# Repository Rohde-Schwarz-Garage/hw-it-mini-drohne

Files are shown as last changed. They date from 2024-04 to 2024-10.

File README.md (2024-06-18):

# BAUEN EINER KLEINEN DROHNE :helicopter:
<!--- Trennbalken bei Überschriften Level 1 (#) + kann kopiert werden --->


<!--- Hier kommt ein schönes Bild + ggf. mehr im Text --->
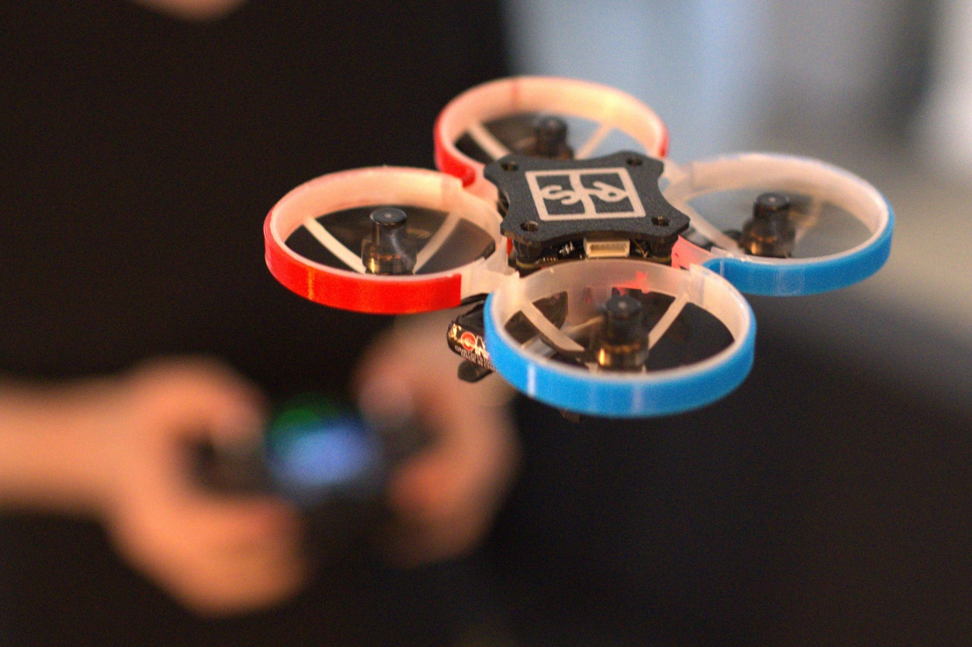
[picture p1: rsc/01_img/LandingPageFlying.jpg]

<!-- ![image](/rsc/01_img/LandingPage.jpg) -->

# Verantwortlichkeiten
<!--- Trennbalken bei Überschriften Level 1 (#) + kann kopiert werden --->


Ausbildung Fachinformatik, LJ2023

# Beschreibung
<!--- Trennbalken bei Überschriften Level 1 (#) + kann kopiert werden --->


In diesem Projekt wirst du eine kleine Drohne bauen. Dazu beschäftigst du dich mit dem Zusammenbau der Komponenten sowie der verwendeten Software und dem anschließenden Tuning. Das Endziel wird es sein, dass die Drohne eigenständig fliegt und von dir einfach gesteuert werden kann.

**Dauer des Projekts:** ca. 1 Arbeitstag, wenn du das Projekt vor Ort in der Garage machst

# Grundlegende Informationen
## Sicherer Umgang mit LiPo-Akkus

>Lithium-Polymer-Akkus, allgemein bekannt als LiPo-Akkus, sind die bevorzugte Energiequelle für die meisten Drohnen aufgrund ihrer hohen Energiedichte und ihrer Fähigkeit, hohe Stromstärken bereitzustellen. Diese Aspekte ermöglichen im Vergleich zu anderen Akkutypen eine längere Flugzeit und eine bessere Performance. 

>Obwohl LiPos viele Vorteile bieten, bringen sie auch spezifische Risiken mit sich. LiPo-Akkus sind sehr empfindlich gegenüber Fehlbehandlungen und können bei falscher Lagerung, falschem Laden oder Tiefentladung Schaden nehmen. Im schlimmsten Fall können diese Akkus sogar Feuer fangen oder explodieren. Daher sind beim Umgang bestimmte Sicherheitsmaßnahmen zu beachten.

### Wichtige Aspekte, die es zu befolgen gilt:

- **Aufladen:** Benutze immer ein Ladegerät, das speziell für LiPo-Akkus ausgelegt ist und lasse die Akkus während des Ladens nicht unbeaufsichtigt. Hier verwenden wird das VIFLY WhoopStor 3 Ladegerät. Bei diesem muss vor dem Aufladen eine **Ladespannung von 4,35V** und eine **Stromstärke von 0,5A** eingestellt werden.

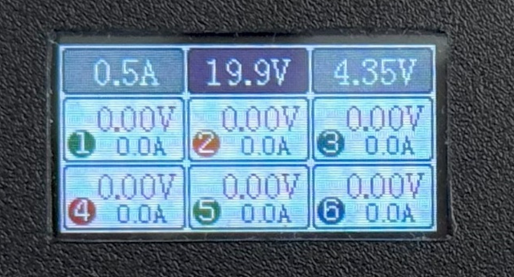
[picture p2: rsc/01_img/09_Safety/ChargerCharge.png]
    

- **Minimale Spannung:** Achte besonders auf die Akkuspannung während des Fliegens. Sollte die Spannung eines Akkus während des Fluges unter den kritischen Wert von 3,5 Volt fallen, muss die Drohne gelandet werden. Die Fernbedienung wird dir ein Warnsignal geben, sobald die Batterie leer ist. Ebenfalls lässt sich in dem „Telemetry-Display“ der Fernbedienung der Ladestand als Balken anzeigen

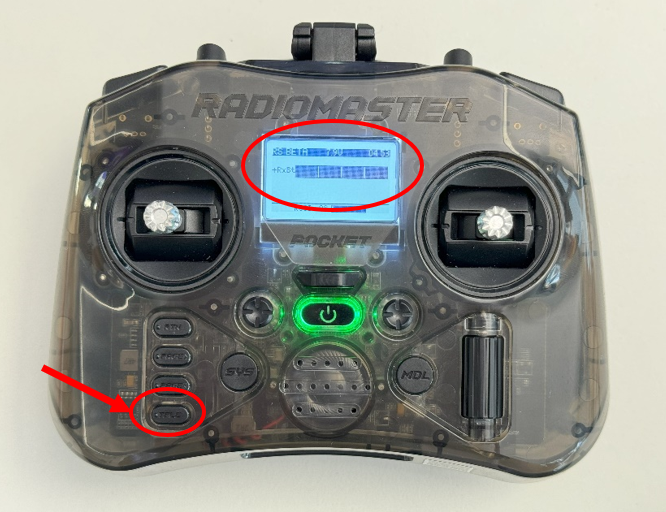
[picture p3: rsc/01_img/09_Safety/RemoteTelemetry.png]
    

- **Lagerzeit:** Vermeide es, die Akkus über einen längeren Zeitraum (maximal 3 Tage) vollständig geladen oder entladen zu lagern, da dies ihre Leistungsfähigkeit und Lebensdauer erheblich beeinträchtigen kann.

- **Lagerspannung:** LiPo-Akkus sollten niemals vollständig geladen oder entladen gelagert werden. Eine optimale Lagerspannung liegt bei ca. 3,8 Volt pro Zelle. Dies bedeutet, dass du die Akkus nach jedem Flug entladen oder vor dem Lagern auf diese Spannung aufladen solltest, wenn du beabsichtigst die Akkus über einen längeren Zeitraum nicht herzunehmen. Dies geschieht mit der Einstellung einer 
**Ladespannung von 3,8V** und einer **Stromstärke von 0,5A**.

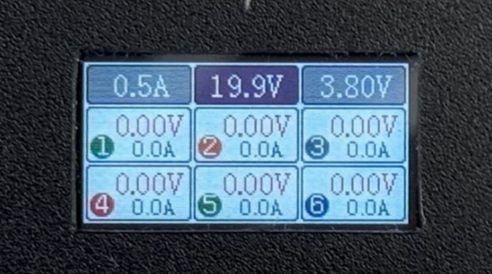
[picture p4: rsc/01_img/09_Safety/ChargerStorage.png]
    

- **Sichere Lagerung:** Um das Risiko im Falle eines Batteriefehlers zu minimieren, solltest du die Akkus immer in einem feuerfesten Behältnis lagern. Dies dient dazu das Restrisiko zu minimieren. Optimal hierfür wäre ein Keramiktopf abgedeckt mit einem Teller. Der Lagerort sollte ebenfalls vor direkter Sonneneinstrahlung geschützt und trocken sein.

Durch Befolgen dieser Sicherheitstipps sorgst du für einen sicheren Umgang mit den LiPo-Akkus deiner Drohne, minimierst potenzielle Gefahren und verlängerst zugleich die Lebensdauer deiner Akkus.

## Was du nach dem Projekt nach Hause nehmen darfst

- Deine fertig gebaute Drohne
- **Einen** Akku (befolge unbedingt die Sicherheitshinweise)
- **In der Garage bleiben:** Ladegerät, Fernsteuerung und Werkzeug 

# Kapitel
<!--- Trennbalken bei Überschriften Level 1 (#) + kann kopiert werden --->


Um zu einer funktionierenden Drohne zu gelangen folge einfach den Kapiteln. Am Ende jedes Kapitels kommst du wieder auf diese Seite.

<!--- Weitere Indexe sind immer möglich --->
1. [Vorbereitung Material und Software](/docs/01_Materials.md)
2. [Zusammenbau Rahmen](/docs/02_FrameAssembly.md)
3. [Navigation und Einrichtung Fernsteuerung](/docs/03_RemoteSetup.md)
4. [Zusammenbau Drohne](/docs/04_DroneAssembly.md)
5. [Einrichtung Flight-Controller](/docs/05_FlightControllerSetup.md)
7. [Testen und Tunen der Drohne](/docs/06_TestingAndTuning.md)
8. [Möglichkeiten zum Ausbau des Projekts](/docs/07_Outlook.md)
9. [Links zu den verwendeten Bauteilen](/docs/08_Links.md)
10. [Sicherheitshinweise](/docs/09_Safety.md)

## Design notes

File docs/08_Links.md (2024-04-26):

# Links zu den verwendeten Bauteilen


## Drohne

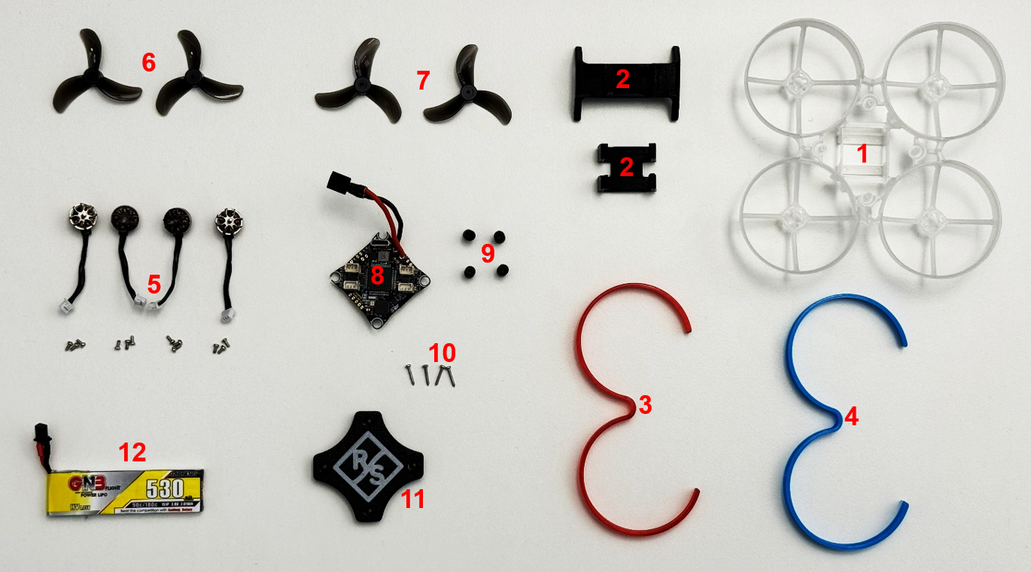
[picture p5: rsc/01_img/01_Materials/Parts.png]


| Bauteil | Anzahl | Nr.  | Link | Alternativ-Link |
|---|---|---|---|---|
| Rahmen | 1 | 1 |[Happymodel Mobula 7 V4 Rahmen](https://www.rotorama.de/product/happymodel-ram-moblite7-v4)|[Happymodel Mobula 7 V4 Rahmen](https://www.drone-fpv-racer.com/en/happymodel-75mm-v4-frame-for-moblite7-8683.html#/10-color-white)|
| Standfuß (zweiteilig) | 1 | 2 |[PETG Schwarz 3D-Druck](https://www.conrad.de/de/p/polymaker-pb01001-polylite-filament-petg-hitzebestaendig-hohe-zugfestigkeit-1-75-mm-1000-g-schwarz-1-st-2632939.html)|[PETG Schwarz 3D-Druck](https://www.reichelt.de/filament-polylite-petg-1-75-mm-1-kg-schwarz-polymaker-b01001-p323881.html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)|
| Markierung rot | 1 | 3 |[TPU Rot 3D-Druck](https://www.conrad.de/de/p/polymaker-pd01003-polyflex-tpu-95a-filament-tpu-flexibel-1-75-mm-750-g-rot-1-st-2632898.html)|[TPU Rot 3D-Druck](https://www.reichelt.de/filament-tpu-92a-rot-1-75-mm-750-g-kimya-pe1014tq-p351400.html?&trstct=vrt_pdn&nbc=1)|
| Markierung blau | 1 | 4 |[TPU Blau 3D-Druck](https://www.conrad.de/de/p/polymaker-pd01005-polyflex-tpu-95a-filament-tpu-flexibel-1-75-mm-750-g-blau-1-st-2632896.html)|[TPU Blau 3D-Druck](https://www.reichelt.de/filament-tpu-92a-blau-1-75-mm-750-g-kimya-pe1015tq-p351401.html?&trstct=vrt_pdn&nbc=1)|
| Motoren (inkl. Schrauben) | 4 | 5 |[Happymodel RS0802 20000Kv](https://www.rotorama.de/product/happymodel-rs0802-20000kv)|[BetaFPV 1102 22000KV Brushless Motor (4pcs)](https://n-factory.de/BetaFPV-1102-22000KV-Brushless-Motor-4pcs)|
| Propeller | 8 | 6,7  |[Gemfan 40mm-3 1608 (1,5mm 8Stk)](https://www.rotorama.de/product/gemfan-40mm-3-1608-1-5mm)|[Gemfan 40mm-3 1608 (1,5mm 8Stk)](https://shop.rc-hangar15.de/Gemfan-40mm-3-Blatt-Propeller-1608-15mm-Welle-clear-black)|
| Flight Controller (FC) mit A30 Stecker| 1 | 8 |[Happymodel CrazyF405 HD 1-2S 12A AIO (FC+ESC+ELRS RX)](https://www.rotorama.de/product/happymodel-crazyf405-hd-aio-fc-esc-elrs-rx)|[Happymodel CrazyF405 HD 1-2S 12A AIO (FC+ESC+ELRS RX)](https://www.drone-fpv-racer.com/en/crazyf405-hd-elrs-12a-aio-by-happymodel-11297.html)|
| Gummi-Abstandshalter | 4 | 9 |Bei Flight Controller enthalten | Bei Flight Controller enthalten |
| Schrauben für Flight Controller | 4 | 10 |Bei Flight Controller enthalten | Bei Flight Controller enthalten |
| R/S Deckplatte | 1 | 11 |[PETG Schwarz 3D-Druck](https://www.conrad.de/de/p/polymaker-pb01001-polylite-filament-petg-hitzebestaendig-hohe-zugfestigkeit-1-75-mm-1000-g-schwarz-1-st-2632939.html)|[PETG Schwarz 3D-Druck](https://www.reichelt.de/filament-polylite-petg-1-75-mm-1-kg-schwarz-polymaker-b01001-p323881.html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)|
| Akku mit A30 Stecker | 2 | 12 |[GNB 530mAh 1S 90C HV A30](https://www.rotorama.de/product/gnb-530mah-1s-90c)|[BONKA 3,8V 1S 450mAh 80C/160C HV BT2.0 Lipo](https://shop.rc-hangar15.de/BONKA-38V-1S-450mAh-80C-160C-HV-BT20-Lipos)
| BT2.0 Pigtail für Flight Controller | 1 |  - |[BT2.0 Pigtail Kabel für 1S](https://shop.rc-hangar15.de/BT20-Pigtail-Kabel-fuer-BT20-1S-1-Stueck-BetaFPV)|[BT2.0 Pigtail Kabel für 1S](https://shop.rc-hangar15.de/BT20-U-Pigtail-Kabel-fuer-BT20-1S-1-Stueck-BetaFPV)|

## Verbrauchsmaterialien

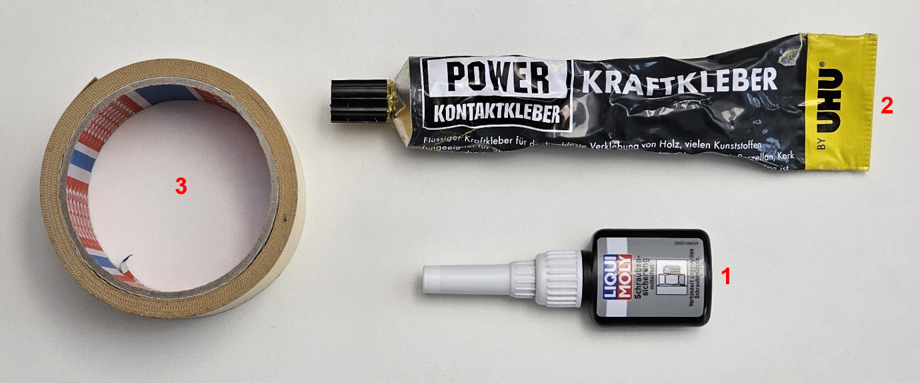
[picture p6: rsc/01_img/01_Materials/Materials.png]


| Material | Nr. | Link | Alternativ-Link |
|---|-----|---|---|
| Schraubensicherung (Loctite) | 1 |[Liqui Moly Schraubensicherung mittelfest](https://www.conrad.de/de/p/liqui-moly-3801-schraubensicherung-festigkeit-mittel-10-g-752960.html)|[Schraubensicherung mittelfest](https://www.reichelt.de/schraubensicherung-lack-mittelfest-blau-10-ml-lack-l310b-p313598.html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)|
| Uhu Kleber Extreme | 2 |[UHU Alleskleber Alleskleber Kraft FLEXTube](https://www.conrad.de/de/p/uhu-alleskleber-alleskleber-kraft-flextube-45040-42-g-478764.html)|[UHU Alleskleber Kraft Flex + Clean](https://www.conrad.de/de/p/uhu-alleskleber-kraft-flex-clean-73-18-g-631774.html#productTechData)|
| Doppelseitiges Klebeband | 3 |[Scotch Transfer-Klebeband Transparent 6mm](https://www.conrad.de/de/p/scotch-924633-924633-transfer-klebeband-transparent-l-x-b-33-m-x-6-mm-1-st-2266070.html)|[Scotch Transfer-Klebeband Transparent 19mm](https://www.conrad.de/de/p/scotch-9241933-9241933-transfer-klebeband-transparent-l-x-b-33-m-x-19-mm-1-st-2266071.html)|

## Werkzeug und Zubehör

Die Fernsteuerung und das Ladegerät, die du für dieses Projekt benötigst, sind qualitativ hochwertige, langlebige Geräte, die sich für eine Vielzahl weiterer Projekte rund um ferngesteuerte Modelle oder Drohnen eignen. Diese Komponenten stellen somit keine Einweginvestition dar, sondern sollten als langfristige Investition in dein Hobby gesehen werden. 

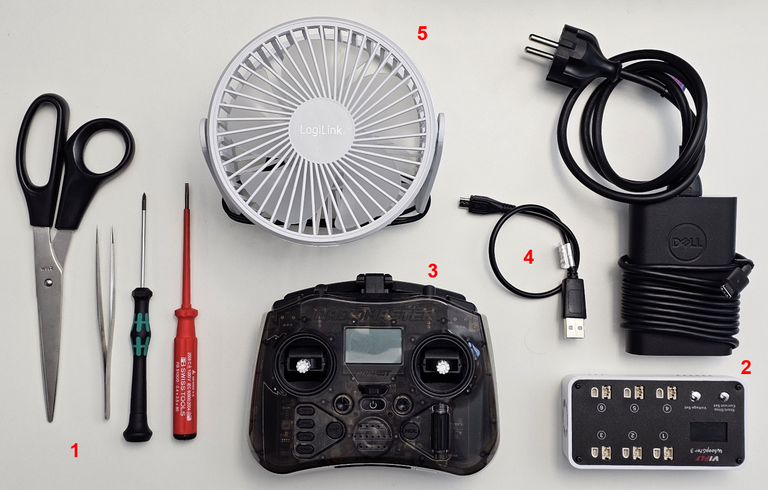
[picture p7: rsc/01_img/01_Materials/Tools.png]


| Werkzeug | Nr. | Link | Alternativ-Link |
|---|-----|---|---|
| Werkzeugwagen in der Garage (Schraubenzieher, Pinzetten, Zangen…) | 1 |Du solltest das benötigte Werkzeug bei dir zu Hause finden. ALternativ findest du in der Garage alles vor, was du brauchst.| - |
| Ladegerät | 2 |[Vifly WhoopStor 3](https://www.rotorama.de/product/vifly-whoopstor)| [Vifly WhoopStor 3](https://shop.rc-hangar15.de/VIFLY-WhoopStor-V3-1S-Lade-Entladegeraet-BT20-PH20-Schwarz)|
| USB-C Netzteil | 2 |[VOLTCRAFT CNPS-45 USB-Ladegerät 45 W](https://www.conrad.de/de/p/voltcraft-cnps-45-usb-ladegeraet-45-w-steckdose-ausgangsstrom-max-3-a-anzahl-ausgaenge-1-x-usb-c-buchse-usb-power-del-1601915.html)|[goobay USB-C PD Dual-Schnellladegerät 45 Watt](https://www.alternate.de/goobay/USB-C-PD-Dual-Schnellladeger%C3%A4t-45-Watt/html/product/100032651)|
| Fernbedienung | 3 |[Radiomaster Pocket ELRS](https://www.rotorama.de/product/radiomaster-pocket-elrs)|[Radiomaster Pocket ELRS](https://shop.rc-hangar15.de/Radiomaster-POCKET-ELRS-Fernsteuerung-EU-LBT-Anthrazit-MODE-1)|
| 18650 Li-Ion-Batterien (2-Stück) | - |[Samsung INR18650-35E 3400mAh 8A - Reclaimed](https://www.rotorama.de/product/samsung-inr18650-35e-3450mah-8a-reclaimed)|[BMZ TerraE INR 18650 30E](https://www.conrad.de/de/p/bmz-terrae-inr-18650-30-e-spezial-akku-18650-li-ion-3-7-v-3000-mah-2481710.html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)|
| Kabel USB-A auf Micro-USB | 4 |[Renkforce USB-Kabel USB 2.0 USB-A Stecker, USB-Micro-B Stecker 1.00 m](https://www.conrad.de/de/p/renkforce-usb-kabel-usb-2-0-usb-a-stecker-usb-micro-b-stecker-1-00-m-schwarz-vergoldete-steckkontakte-rf-4316220-1438740.html)|[goobay USB 2.0 Kabel](https://www.alternate.de/goobay/USB-2-0-Kabel-USB-A-Stecker-Micro-USB-Stecker/html/product/1077314)|
| Lüfter | 5 |[LogiLink UA0403 USB-Ventilator](https://www.conrad.de/de/p/logilink-ua0403-usb-ventilator-b-x-h-x-t-180-x-126-x-195-mm-2813812.html)|[LogiLink UA0402 USB-Ventilator](https://www.conrad.de/de/p/logilink-ua0402-usb-ventilator-b-x-h-x-t-140-x-115-x-147-mm-2813811.html)|

## [Klicke hier, um zurück zur Vorbereitung von Material und Software zu kommen!](/docs/01_Materials.md)

## [Klicke hier, um zurück zur Übersicht der Kapitel zu kommen!](/README.md#kapitel)

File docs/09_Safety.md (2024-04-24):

# Sicherheitshinweise


## Vorsicht vor Propellern und Motoren

>Es ist fundamental wichtig, sich der Risiken bewusst zu sein, die von den Propellern und Motoren einer Drohne ausgehen, unabhängig von ihrer Größe. In der Drohnen-Community werden die Drohnen oft treffend als "fliegende Mixer" bezeichnet – und sie können ebenso gefährlich sein.

>Die Propeller können Verletzungen verursachen, wenn sie in Kontakt mit Haaren, Schmuck oder Kleidung kommen. Daher sollte die Drohne immer ausgeschaltet sein, wenn sie nicht aktiv genutzt wird. Darüber hinaus sollte sichergestellt werden, dass sich niemand in der Flugbahn der Drohne oder in der unmittelbaren Umgebung befindet, wenn die Propeller in Bewegung sind. 

Mache dir immer die potenzielle Gefahr bewusst, die von den Propellern und Motoren ausgeht, und stelle die Drohne in eine sichere Umgebung, bevor du mit der Arbeit oder dem Fliegen beginnst. Prävention ist der beste Weg, um sicherzustellen, dass du deine Drohne genießen kannst, ohne dich selbst oder andere zu verletzen.

## Sicherer Umgang mit LiPo-Akkus

>Lithium-Polymer-Akkus, allgemein bekannt als LiPo-Akkus, sind die bevorzugte Energiequelle für die meisten Drohnen aufgrund ihrer hohen Energiedichte und ihrer Fähigkeit, hohe Stromstärken bereitzustellen. Diese Aspekte ermöglichen im Vergleich zu anderen Akkutypen eine längere Flugzeit und eine bessere Performance. 

>Obwohl LiPos viele Vorteile bieten, bringen sie auch spezifische Risiken mit sich. LiPo-Akkus sind sehr empfindlich gegenüber Fehlbehandlungen und können bei falscher Lagerung, falschem Laden oder Tiefentladung Schaden nehmen. Im schlimmsten Fall können diese Akkus sogar Feuer fangen oder explodieren. Daher sind beim Umgang bestimmte Sicherheitsmaßnahmen zu beachten.

### Wichtige Aspekte, die es zu befolgen gilt:

- **Aufladen:** Benutze immer ein Ladegerät, das speziell für LiPo-Akkus ausgelegt ist und lasse die Akkus während des Ladens nicht unbeaufsichtigt. Hier verwenden wird das VIFLY WhoopStor 3 Ladegerät. Bei diesem muss vor dem Aufladen eine **Ladespannung von 4,35V** und eine **Stromstärke von 0,5A** eingestellt werden.

    

- **Minimale Spannung:** Achte besonders auf die Akkuspannung während des Fliegens. Sollte die Spannung eines Akkus während des Fluges unter den kritischen Wert von 3,5 Volt fallen, muss die Drohne gelandet werden. Die Fernbedienung wird dir ein Warnsignal geben, sobald die Batterie leer ist. Ebenfalls lässt sich in dem „Telemetry-Display“ der Fernbedienung der Ladestand als Balken anzeigen

    

- **Lagerzeit:** Vermeide es, die Akkus über einen längeren Zeitraum (maximal 3 Tage) vollständig geladen oder entladen zu lagern, da dies ihre Leistungsfähigkeit und Lebensdauer erheblich beeinträchtigen kann.

- **Lagerspannung:** LiPo-Akkus sollten niemals vollständig geladen oder entladen gelagert werden. Eine optimale Lagerspannung liegt bei ca. 3,8 Volt pro Zelle. Dies bedeutet, dass du die Akkus nach jedem Flug entladen oder vor dem Lagern auf diese Spannung aufladen solltest, wenn du beabsichtigst die Akkus über einen längeren Zeitraum nicht herzunehmen. Dies geschieht mit der Einstellung einer 
**Ladespannung von 3,8V** und einer **Stromstärke von 0,5A**.

    

- **Sichere Lagerung:** Um das Risiko im Falle eines Batteriefehlers zu minimieren, solltest du die Akkus immer in einem feuerfesten Behältnis lagern. Dies dient dazu das Restrisiko zu minimieren. Optimal hierfür wäre ein Keramiktopf abgedeckt mit einem Teller. Der Lagerort sollte ebenfalls vor direkter Sonneneinstrahlung geschützt und trocken sein.

Durch Befolgen dieser Sicherheitstipps sorgst du für einen sicheren Umgang mit den LiPo-Akkus deiner Drohne, minimierst potenzielle Gefahren und verlängerst zugleich die Lebensdauer deiner Akkus.

## [Klicke hier, um zurück zum Zusammenbau des Rahmens zu kommen!](/docs/02_FrameAssembly.md#akku-laden)

## Sicheres Fliegen

Beim Fliegen deiner Drohne ist es unerlässlich, dass du jederzeit volle Kontrolle und Überblick hast. Empfehlenswert ist es vor allem in geschlossenen Räumen zu fliegen, um jegliches Risiko zu vermeiden, dass die Drohne außer Sicht gerät.

Ein wichtiger Aspekt bei der Bedienung deiner Drohne ist das Verständnis des Start- und Stoppvorgangs. Zum Starten der Drohne sind folgende Schritte erforderlich: Stelle sicher, dass der **Schub auf null (1)** reduziert ist und raste dann den ***Arm*-Button (2)** ein. Dies aktiviert die Motoren und lässt die Drohne abheben. 

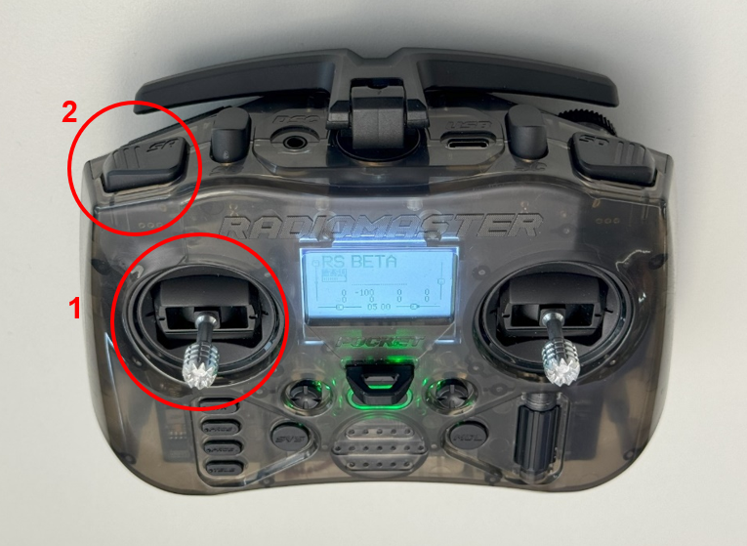
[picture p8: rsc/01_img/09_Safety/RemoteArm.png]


Sollte während des Flugs etwas Unvorhersehbares passieren oder du möchtest einfach die Drohne landen, drücke den ***Arm*-Button** erneut, um die Motoren sofort zu stoppen, auch bekannt als ***Disarm***. Dies stoppt alle Motoren und lässt die Drohne sofort landen.

Es ist wichtig, diese Prozedur immer im Hinterkopf zu behalten, um auf unvorhergesehene Ereignisse schnell reagieren zu können und um allen Anwesenden ein hohes Maß an Sicherheit zu gewährleisten. Fliege immer verantwortungsbewusst und stelle sicher, dass du deine Drohne jederzeit im Blick hast. Durch Beachtung dieser Hinweise wird das Fliegen zu einem sicheren und spaßigen Erlebnis.

## [Klicke hier, um zurück zum Zusammenbau der Drohne zu kommen!](/docs/04_DroneAssembly.md#hinweis)

## [Klicke hier, um zurück zum Setup des Flight-Controllers zu kommen!](/docs/05_FlightControllerSetup.md#konfiguration-motorsteuerung)

## [Klicke hier, um zurück zur Übersicht der Kapitel zu kommen!](/README.md#kapitel)

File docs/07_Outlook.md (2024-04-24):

# Möglichkeiten zum Ausbau des Projekts


## Anpassung der Rates in Betaflight

>Die Rates legen fest, wie schnell die Drohne auf deinen Steuerbefehl reagiert und ein Kippen (Pitch), Rollen (Roll) oder eine Drehung um die eigene Achse (Yaw) vollzieht. Dabei ist die Höhe der Rates proportional zu der Geschwindigkeit, mit der die Drohne diese Bewegungen ausführt. Hohe Rates führen dazu, dass die Drohne schneller in die gewünschte Richtung kippt, rollt oder um die eigene Achse dreht, während geringere Rates entsprechend langsamere Bewegungen bewirken.

>Es ist wichtig zu beachten, dass höhere Rates zwar schnelle und akrobatische Manöver ermöglichen, sie erfordern jedoch auch ein entsprechendes Maß an Erfahrung und Kontrolle beim Fliegen. Anfänger sollten daher eher mit niedrigeren Rates starten und diese langsam steigern, je sicherer sie im Umgang mit der Drohne werden. 

Das Anpassen der Rates ist im *Betaflight Configurator* möglich. Verbinde dazu die Drohne mit deinem Rechner und wechsle in den PID Tuning Tab (1). Dort kannst du in dem Reiter „Ratenprofile anpassen“ (2) Anpassungen an den „RC-Rates“ (3) vornehmen. Vergiss anschließend nicht die Änderungen zu speichern.

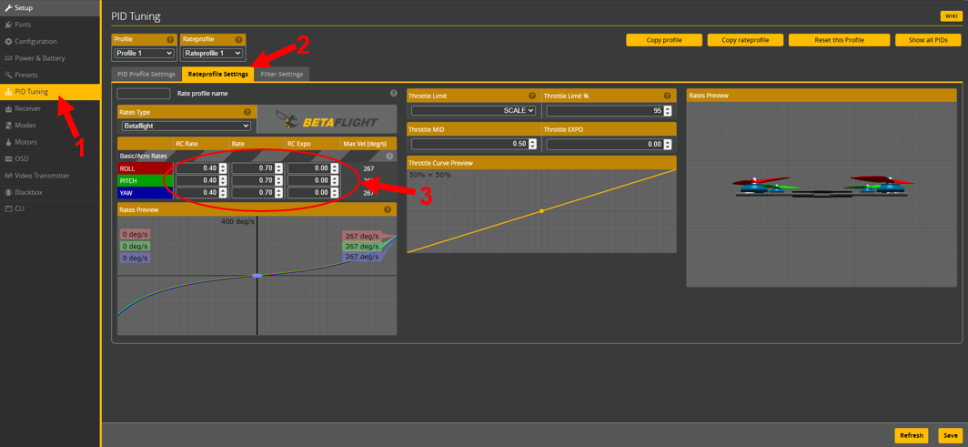
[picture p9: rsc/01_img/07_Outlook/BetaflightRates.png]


Es wird empfohlen, die Rates schrittweise um 0,05 zu erhöhen und anschließend ausgiebig zu testen, wie sich das Flugverhalten deiner Drohne verändert und ob dir dies gefällt.

## Erste Versuche den Acro-Modus zu bändigen

>Die Steuerung im Angle Mode und Acro Mode unterscheidet sich tatsächlich erheblich und beeinflusst das Verhalten und die Reaktionsweise der Drohne auf die Eingaben des Piloten.

>Im Angle Mode versucht die Drohne, ihre Nivellierung beizubehalten. Wenn du einen Steuereingriff ausführen, etwa eine Neigung nach links oder rechts, wird die Drohne nach links oder rechts neigen, aber sobald du den Steuerknüppel freigibst, wird die Drohne automatisch in eine flache, horizontale Position zurückkehren. Dieser Modus versucht, die Drohne stets stabil und ausgeglichen zu halten, was ihn ideal für Anfänger oder für Situationen macht, in denen Stabilität und einfache Steuerung wichtig sind.

>Der Acro Mode hingegen ist viel direkter und bietet dem Piloten volle Kontrolle über die Drohne. In diesem Modus wird die Drohne nicht automatisch stabilisiert oder auf eine horizontale Position zurückgesetzt. Stattdessen bleibt die Drohne in der Position, in die du sie gebracht hast. Wenn du also den Steuerknüppel loslässt, nachdem du die Drohne in eine Neigung versetzt hast, bleibt sie in dieser Neigung und kehrt nicht automatisch in die horizontale Position zurück. Dies erfordert mehr Geschick durch den Piloten, ermöglicht aber auch mehr Kontrolle und Flexibilität bei der Durchführung von Manövern.

### Einrichten des Acro-Modus:

1.	Schalte die Fernsteuerung an und verbinde anschließend die Drohne mit dem Betaflight-Konfigurator

2.	Wechsle in den Modi-Tab im Konfigurator. Hier wählst du zuerst „Nicht benutze Modi ausblenden“ (1) aus und du solltest dann „ANGLE“ sehen.

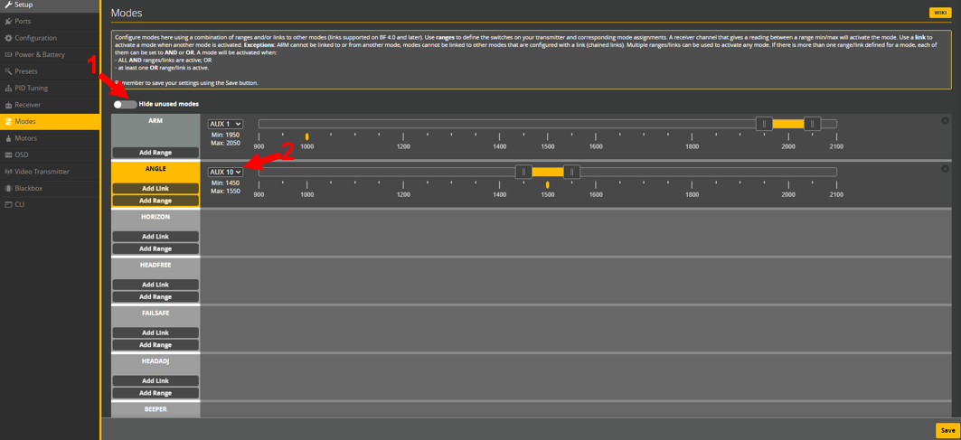
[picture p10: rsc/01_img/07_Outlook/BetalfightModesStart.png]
    

3.	Stelle nun die Schaltfläche, die mit „AUX“ (2) beginnt, auf „AUTO“ um und raste die rechte Schultertaste der Fernsteuerung ein. Die Schaltfläche sollte nun auf einen neuen AUX-Kanal umgesprungen sein. Wenn dies nicht der Fall ist, stelle sicher, dass die Fernsteuerung mit der Drohne verbunden ist.

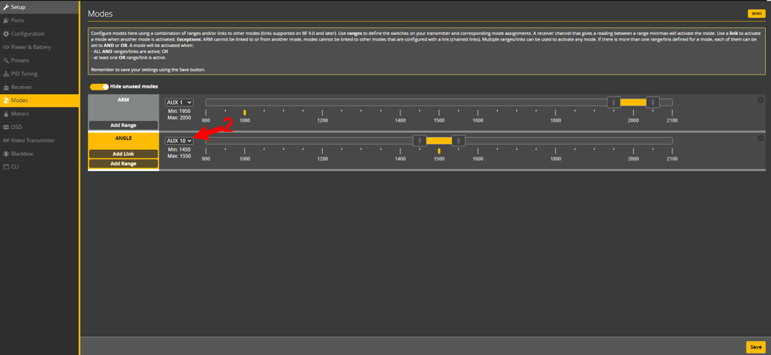
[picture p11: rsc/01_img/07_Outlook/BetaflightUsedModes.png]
    

4.	Raste die rechte Schultertaste nun wieder aus und beobachte, wie sich die kleine gelbe Markierung unter dem Balken verschiebt. Ziehe den darüberliegenden Kasten nun so zurecht, dass er die kleine gelbe Markierung umschließt.

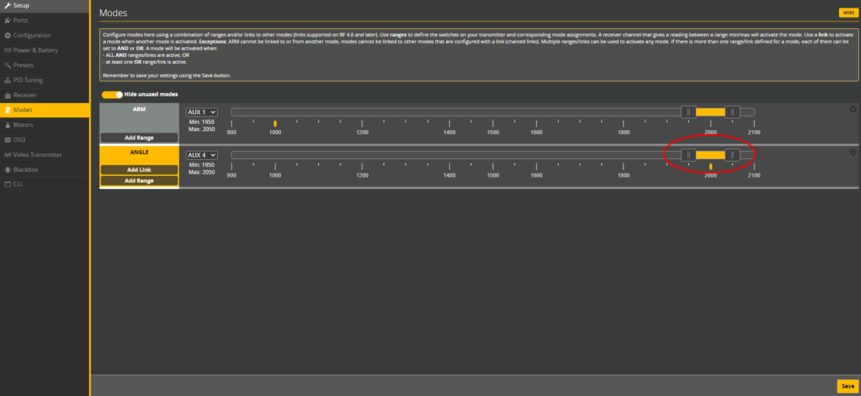
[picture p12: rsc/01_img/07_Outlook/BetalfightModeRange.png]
    

5.	Klicke auf „Speichern“. 

Jetzt kannst du den Acro-Modus aktivieren, indem du die rechte Schultertaste einrastest! Die Beherrschung dieses Flugmodus benötigt sehr viel Geduld und Übung. Es ist zu empfehlen zuerst in einem Simulator am PC oder einer Spielekonsole zu üben. Mehr zu Simulatoren findest du unter weiterführende Quellen. 

## FPV - ein völlig neues Erlebnis

FPV steht für "First Person View", was bedeutet, dass Piloten den Flug ihrer Drohne aus der Vogelperspektive verfolgen können. Dies wird erreicht, indem ein Live-Video-Feed von der Kamera der Drohne direkt zu einem Bildschirm, einer Videobrille, oder einem anderen Display-Gerät des Piloten übertragen wird.

Traditionelle Drohnen werden oft "VLOS" (Visual Line of Sight) geflogen, was bedeutet, dass der Pilot die Drohne ständig im Auge behält und sie aus seiner eigenen Perspektive steuert. Das kann Limitationen mit sich bringen, besonders wenn die Drohne außer Sichtweite gerät oder wenn der Pilot die Ausrichtung der Drohne nicht genau bestimmen kann.

FPV-Systeme nutzen verschiedene Technologien, um das Video von der Drohne zum Piloten zu übertragen. Aktuell werden zwei Methoden unterschieden: analoge und digitale Übertragung.

Analoge FPV-Systeme sind die ältere Technologie und sind wegen ihrer niedrigen Latenz und ihrer robusten Leistung unter schwierigen Bedingungen immer noch weit verbreitet. Sie übertragen das Videosignal ohne Buffering vom Sender in der Drohne zum Empfänger in der Bodenstation des Piloten. Die Qualität des Videosignals bei analogen Systemen ist generell schlechter als bei digitalen Systemen, aber die Verzögerung des Signals (die sogenannte Latenz) ist typischerweise sehr gering und konstant. Dies ist besonders wichtig beim Fliegen mit hohen Geschwindigkeiten oder bei komplexen Manövern, da selbst eine geringfügige Verzögerung zu einem Absturz führen kann.

Digitale FPV-Systeme dagegen bieten eine höhere Videoqualität, indem sie das Videosignal digital kodieren und übertragen. Das führt zu einem schärferen Bild mit mehr Details, was insbesondere bei komplexen Flugumgebungen oder beim Fliegen auf größere Distanzen nützlich sein kann. Aber digitale Systeme haben tendenziell eine höhere Latenz als analoge, was sie weniger geeignet für Rennsport oder Fliegen unter extremen Bedingungen macht. 

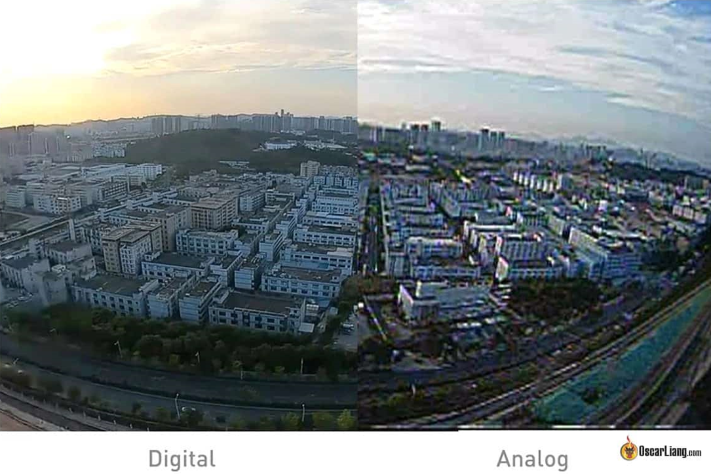
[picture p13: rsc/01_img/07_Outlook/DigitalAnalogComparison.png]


Jüngste Entwicklungen in der FPV-Technologie zielen darauf ab, die hohe Bildqualität der digitalen Systeme mit der geringen Latenz der analogen Systeme zu kombinieren. Diese neuen Systeme verwenden fortschrittliche Kodierungstechniken und spezielle Hardware, um digitale Videoübertragungen mit minimalem Zeitverzug zu ermöglichen. Es gilt jedoch zu beachten, dass die digitalen Systeme in der Regel deutlich teurer sind als traditionelle analoge Systeme.

Wenn du mehr über FPV erfahren willst, kannst du dich in den weiterführenden Quellen nach Belieben informieren.

## Weiterführende Quellen

Wenn du gerne noch mehr über Drohnen und insbesondere FPV-Drohnen wissen möchtest können wir dir folgende Quellen herzlichst empfehlen:

### [How To Get Started With FPV Drones](https://oscarliang.com/fpv-drone-guide/)

Ein wunderbarer Blog, der in sehr gut recherchierten und umfassenden Texten alles um das Thema Drohnen erklärt. Seien es Tipps für den Einstieg, technische Hintergründe oder empfehlenswerte Produkte. Es ist ausdrücklich erwünscht auf der Seite zu stöbern!

### [Leran to fly an FPV drone](https://www.youtube.com/watch?v=SpuXqNakP2A&list=PLwoDb7WF6c8lCKhQOTy-Vb9LfW0VAIrTP)

Mit diesem Guide kannst du deine Flugfertigkeiten verfeinern. Nutze dazu einfach deine Fernsteuerung und schließe sie an deinem PC an. Schon kannst du in einem Simulator (mehr dazu später) üben, ohne echte Drohnen abstürzen zu lassen.

Joshua Bardwell ist in der Community hoch angesehen für seine informativen Videos und Tutorials. Stöbern lohnt sich also auch hier.

### [Liftoff® Simulator](https://store.steampowered.com/app/410340/Liftoff_FPV_Drone_Racing/)

Mit diesem Simulator kannst du in vielfältigen Umgebungen die unterschiedlichsten FPV-Drohnen fliegen und im Multiplayer Rennen fliegen. Die Simulatoren sind mittlerweile so gut, dass sich die Erfahrung problemlos auf echte Drohnen übertragen lässt.

Ein Simulator ist sehr gut angelegtes Geld. Jeden Unfall, den du im Simulator baust, spart dir Geld für Ersatzteile an einer echten Drohne.

### [quadmovr - YouTube](https://www.youtube.com/@quadmovr/videos)

Man braucht kein FPV um eine Drohne akrobatisch zu fliegen. Auf diesem YouTube-Kanal findest du beeindruckende und vielleicht sogar inspirierende Beispiele dafür.

### [EU Drohnenverordnung 2024](https://www.drohnen.de/47366/eu-drohnenverordnung-2024/)

Hier findest du gesetzliche Regelungen für den Umgang mit Drohnen. Du solltest dich mit diesen auseinandersetzen, bevor du im Freien fliegst.

## [Klicke hier, um zurück zur Übersicht der Kapitel zu kommen!](/README.md#kapitel)

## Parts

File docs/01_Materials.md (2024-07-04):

# Vorbereitung Material und Software


In diesem Abschnitt findest du alles, was du benötigst, um dieser Anleitung folgen zu können. Die Links zu dem verwendeten Material findest du [hier](/docs/08_Links.md).

## Bauteile



| Bauteil | Anzahl | Nr.  |
|---|---|---|
| Rahmen | 1 | 1 |
| Standfuß (zweiteilig) | 1 | 2 |
| Markierung rot | 1 | 3 |
| Markierung blau | 1 | 4 |
| Motoren (inkl. Schrauben) | 4 | 5 |
| Propeller (Drehrichtung rechts) | 2 | 6 |
| Propeller (Drehrichtung links) | 2 | 7 |
| Flight Controller (FC) mit A30 Stecker| 1 | 8 |
| Gummi-Abstandshalter | 4 | 9 |
| Schrauben für Flight Controller | 4 | 10 |
| R/S Deckplatte | 1 | 11 |
| Akku mit A30 Stecker | 2 | 12 |

### Hinweis Akku

Der Akku befindet sich in einem sogenannten Safe Bag (im Bild zu sehen) und wird von Beuteln mit feuerhemmendem Material abgedeckt. Den Safe Bag findest du im weißen Schrank unter dem linken Fenster der Garage.

Nach Verwendung des Akkus lege ihn bitte wieder in den Safe Bag und verschließe den diesen ordnungsgemäß. Mehr über den sicheren Umgang mit Akkus findest du [hier](/docs/09_Safety.md#sicherer-umgang-mit-lipo-akkus).



## Verbrauchsmaterialien



| Material | Nr. |
|---|-----|
| Schraubensicherung (Loctite) | 1 |
| Uhu Kleber Extreme | 2 |
| Doppelseitiges Klebeband | 3 |

## Werkzeug und Zubehör



| Werkzeug | Nr. |
|---|-----|
| Werkzeugwagen in der Garage (Schraubenzieher, Pinzetten, Zangen…) | 1 |
| Ladegerät mit Netzteil | 2 |
| Fernbedienung (EdgeTX v2.10) mit eingelegten 18650 Li-Ion-Batterien | 3 |
| Kabel USB-A auf Micro-USB | 4 |
| Lüfter | 5 |

# Software


| Software | Link |
|---|---|
| Betaflight Configurator (Version 10.9.0)  | [Klicke hier](https://github.com/betaflight/betaflight-configurator/releases) |
| ExpressLRS Configurator (Version 1.6.1) | [Klicke hier](https://github.com/ExpressLRS/ExpressLRS-Configurator/releases) |
| ESC-Configurator WebUI | [Klicke hier](https://esc-configurator.com/)  |
| STM32 Virtual COM Port Driver | [Klicke hier](https://www.st.com/en/development-tools/stsw-stm32102.html) |
| Zadig USB Driver Installer | [Klicke hier](https://zadig.akeo.ie/) |
| EdgeTX Buddy | [Klicke hier](https://buddy.edgetx.org/#/flash?version=v2.10.2)

## Installation Betaflight Konfigurator

Ab hier beginnt die Anleitung. Folge ihr Schritt für Schritt, um zum Schluss das gewünschte Ergebnis zu erzielen.  
> Generell versucht die Anleitung möglichst geradlinig zum Ziel „Du steuerst und fliegst die Drohne“ zu kommen. Wenn du aber verstehen möchtest, warum dabei gerade ein Schritt so gemacht wird, wie er gemacht wird, dann sind fast überall in der Anleitung eingerückte Kästen zu finden. Dort werden genau diese Hintergründe beleuchtet.

1.	Öffne den Link und lade die Version 10.9.0 in der passenden Version für dein Betriebssystem herunter (für 64bit Windows: betaflight-configurator_10.9.0_win64-installer.exe)

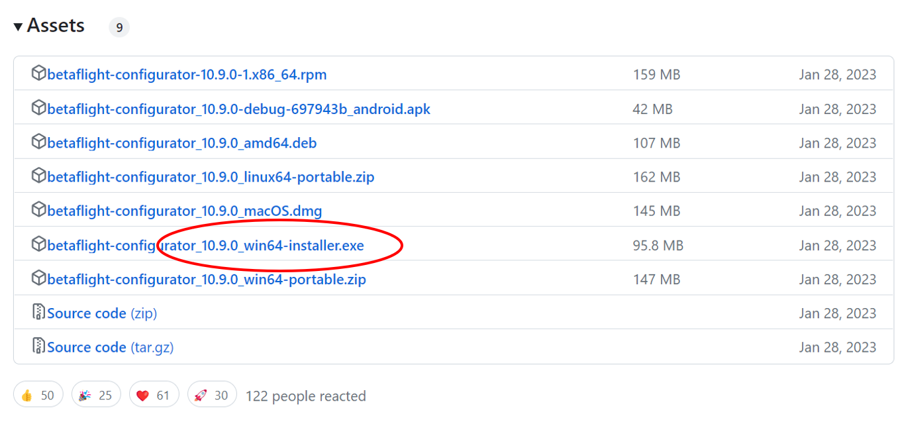
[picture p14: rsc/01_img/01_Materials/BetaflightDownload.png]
    
2.	Führe die heruntergeladene Datei aus und folge den Anweisungen. Nach dem Fertigstellen kannst du den Konfigurator gleich wieder schließen, falls dieser sich geöffnet hat

## Installation ExpressLRS Konfigurator

1.	Öffne den Link und lade die Version 1.6.1 in der passenden Version für dein Betriebssystem herunter (für 64bit Windows: ExpressLRS-Configurator-Setup-1.6.1.exe)

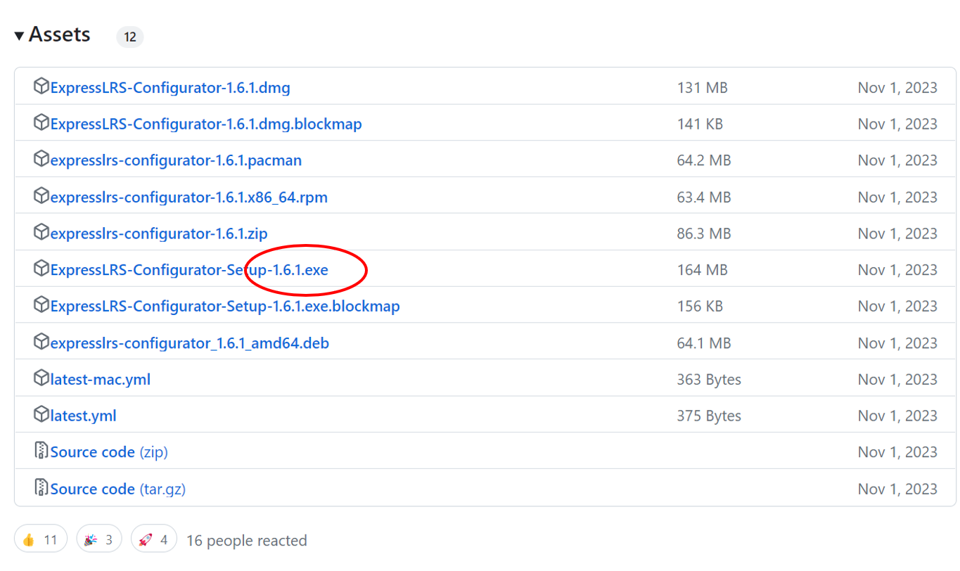
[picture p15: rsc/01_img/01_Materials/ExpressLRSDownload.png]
    
2.	Führe die heruntergeladene Datei aus und folge den Anweisungen. Nach dem Fertigstellen kannst du den Konfigurator gleich wieder schließen, falls dieser sich geöffnet hat

## Installation STM32 Virtual COM Port Treiber

1.	Öffne den Link zur Herstellerseite und klicke auf „Get Latest“

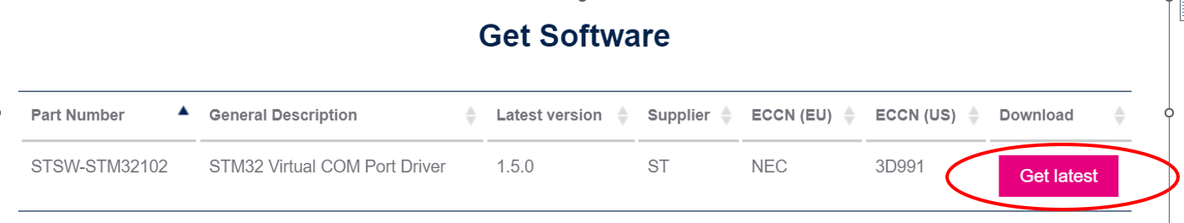
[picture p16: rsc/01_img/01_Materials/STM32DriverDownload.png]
    
2.	Akzeptiere die Lizenzbestimmungen und klicke auf „Download as a guest“
3.	Nach dem Ausfüllen und Abschicken erhältst du eine E-Mail mit einem Download-Link. Mit diesem gelangst du wieder auf die Website und es wird automatisch ein komprimierter Ordner mit dem Treiber heruntergeladen
4.	Entpacke den ZIP-Ordner und führe „VCP_V1.5.0_Setup_W8_x64_64bits.exe“ aus, wenn du ein 64bit Betriebssystem mit mindestens Windows 8 hast
5.	Folge dem Wizard und denke dir einen schönen Firmennamen aus, damit du mit der Installation fortfahren kannst

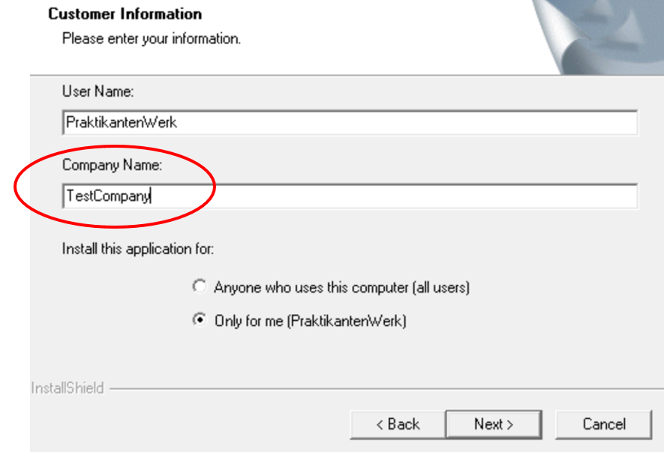
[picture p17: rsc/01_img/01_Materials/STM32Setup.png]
    
6.	Folge allen weiteren Anweisungen
7.	Starte deinen PC neu, damit der Treiber vollständig installiert ist

## Installation Zadig USB Treiber

1.	Öffne den Link und lade die neueste Version von Zadig herunter
2.	Wenn du an späteren Stellen in der Anleitung auf Probleme bei Installationen stößt, wirst du an diese Stelle verwiesen und kannst fehlende Treiber installieren.
3.	Öffne dafür die heruntergeladene zadig.exe und klicke auf „Install Diver“

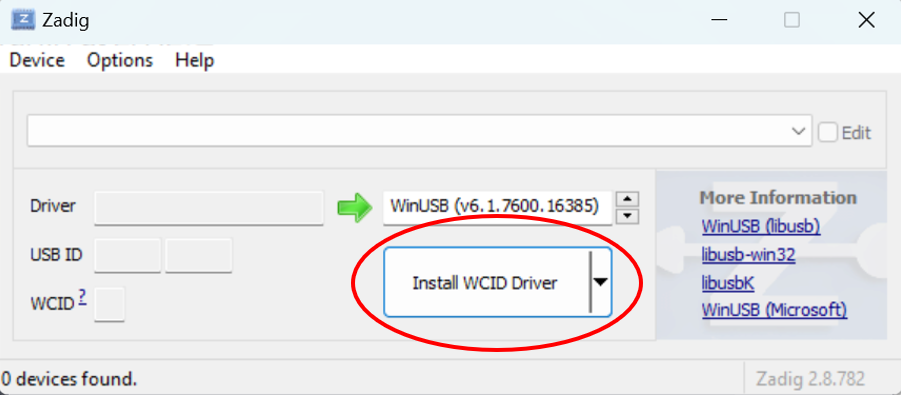
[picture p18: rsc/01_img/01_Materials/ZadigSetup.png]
    
4.	Sollte nach diesem Schritt es immer noch nicht funktionieren kannst du deinen PC neustarten.

## [Klicke hier, um zurück zur Übersicht der Kapitel zu kommen!](/README.md#kapitel)

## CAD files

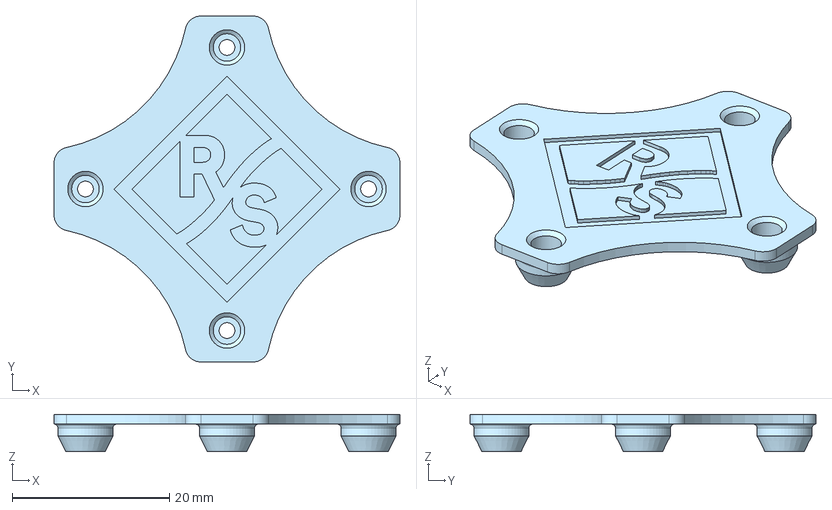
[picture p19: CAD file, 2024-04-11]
rsc/02_printing/01_SingleMaterial/01_STEP/Deckplatte.step
44.0 x 44.0 x 4.75 mm

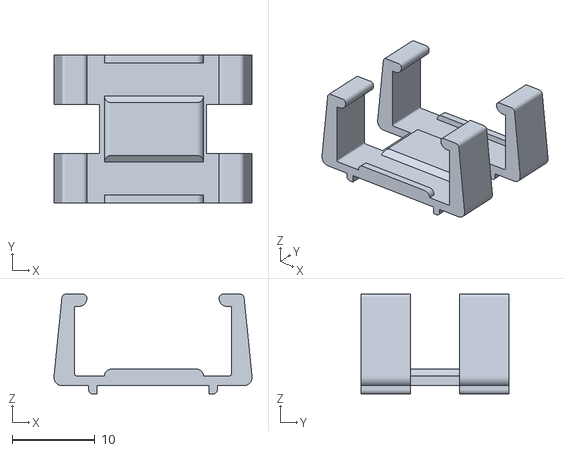
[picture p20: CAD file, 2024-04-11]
rsc/02_printing/01_SingleMaterial/02_STL/Standfuss2.stl
24.0 x 18.0 x 12.1

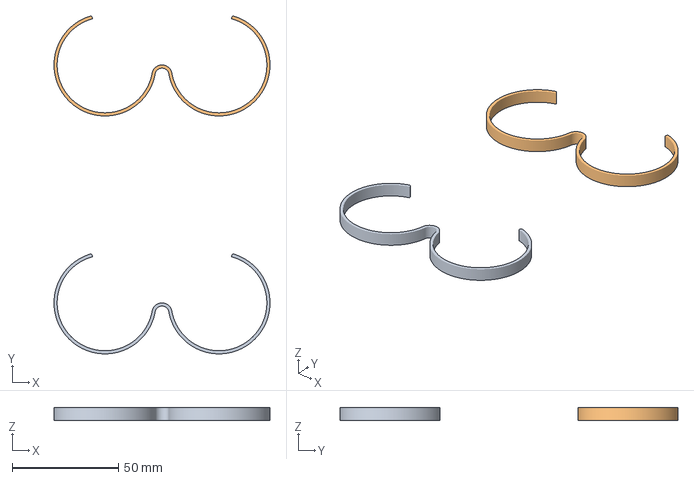
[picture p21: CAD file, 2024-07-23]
rsc/02_printing/01_SingleMaterial/03_3mf/Markierung_TPU_CreatBotF430.3mf
101.7 x 159.0 x 6.00 mm
Markierung.step x 2

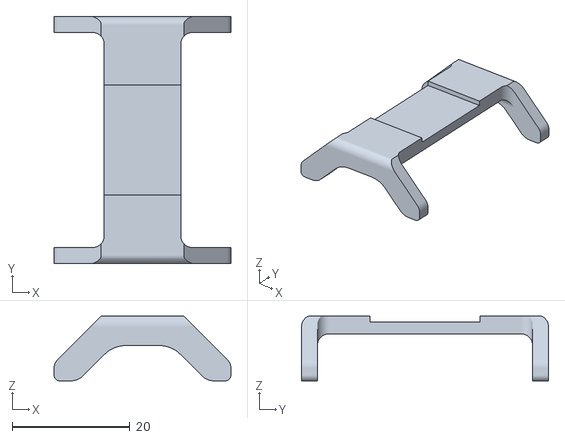
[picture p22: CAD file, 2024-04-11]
rsc/02_printing/01_SingleMaterial/02_STL/Standfuss1.stl
30.0 x 41.9 x 11.0

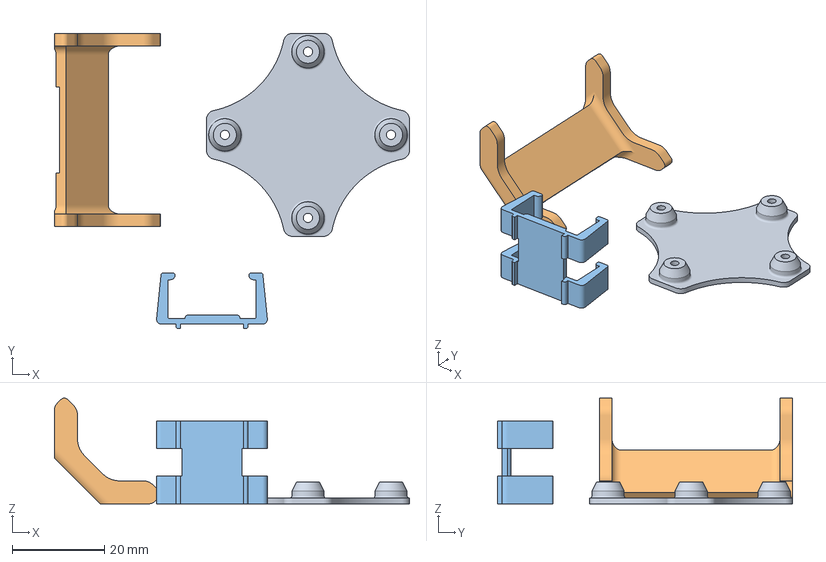
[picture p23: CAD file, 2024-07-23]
rsc/02_printing/01_SingleMaterial/03_3mf/StandfussDeckplatte_ABSPlus_CreatBotF430.3mf
76.9 x 64.0 x 22.9 mm
Deckplatte.step
Standfuss1.step
Standfuss2.step

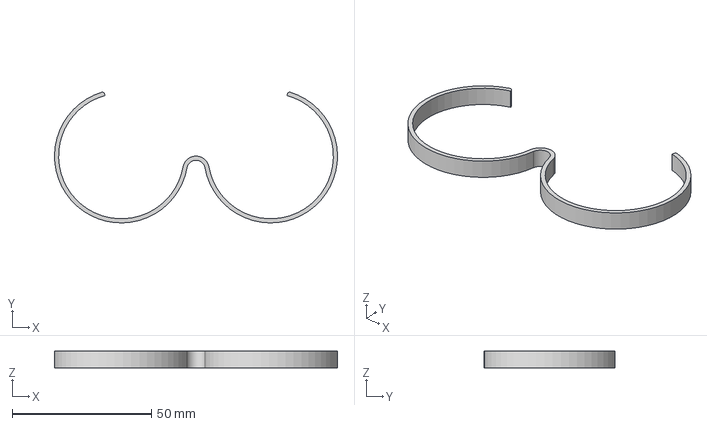
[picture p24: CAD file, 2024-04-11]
rsc/02_printing/01_SingleMaterial/01_STEP/Markierung.step
101.6 x 47.0 x 6.00 mm

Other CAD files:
rsc/02_printing/02_MultiMaterial/01_STEP/Deckplatte.step
rsc/02_printing/02_MultiMaterial/02_STL/Deckplatte.stl
rsc/02_printing/01_SingleMaterial/01_STEP/Standfuss2.step
rsc/02_printing/02_MultiMaterial/01_STEP/Standfuss1.step
rsc/02_printing/01_SingleMaterial/02_STL/Markierung.stl
rsc/02_printing/01_SingleMaterial/03_3mf/StandfussDeckplatte_PETG_CreatbotF430.3mf
rsc/02_printing/02_MultiMaterial/02_STL/Markierung.stl
rsc/02_printing/01_SingleMaterial/01_STEP/Standfuss1.step
rsc/02_printing/01_SingleMaterial/02_STL/Deckplatte.stl
rsc/02_printing/01_SingleMaterial/03_3mf/Markierung_TPU_MK3S.3mf
rsc/02_printing/01_SingleMaterial/03_3mf/Markierung_ABSPlus_MK3S.3mf
rsc/02_printing/01_SingleMaterial/03_3mf/Markierung_PETG_MK3S.3mf
rsc/02_printing/01_SingleMaterial/03_3mf/StandfussDeckplatte_ABSPlus_MK3S.3mf
rsc/02_printing/01_SingleMaterial/03_3mf/StandfussDeckplatte_PETG_MK3S.3mf
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

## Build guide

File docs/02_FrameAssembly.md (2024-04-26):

# Zusammenbau Rahmen


## Grundlegende Komponenten einer Drohne

Im Kern ist eine Drohne ziemlich simpel: Es gibt eine Energiequelle, den Akku. Aus diesem wird die Energie entnommen und über die ESCs (Electronic Speed Controller), die auf der Platine des Flight Controllers sitzen, an die vier Motoren geschickt. Die Motoren treiben die Propeller an, die wiederum für Auftrieb sorgen, sodass die Drohne abheben und fliegen kann. Aerodynamisch funktioniert sie im Grunde wie ein Helikopter, nur statt einem großen Rotor hat sie eben vier kleinere Propeller.

Die Steuerung des ganzen übernimmt der Flight Controller. Er ist das Gehirn der Drohne. Seine Befehle erhält er von der Fernbedienung, die du in der Hand hältst.  
In der Fernbedienung integriert ist ein Übertragungs- bzw. Sendemodul. Auf dem Flight Controller sitzt das Gegenstück dazu, das Empfangsmodul. Über diese Module hinweg erfolgt die Kommunikation zwischen Fernbedienung und dem Flight Controller auf der Drohne.

**Legende:** 
<code style="color : Cyan">Kommunikation/Steuerung</code>
<code style="color : Orangered">Energiefluss</code>

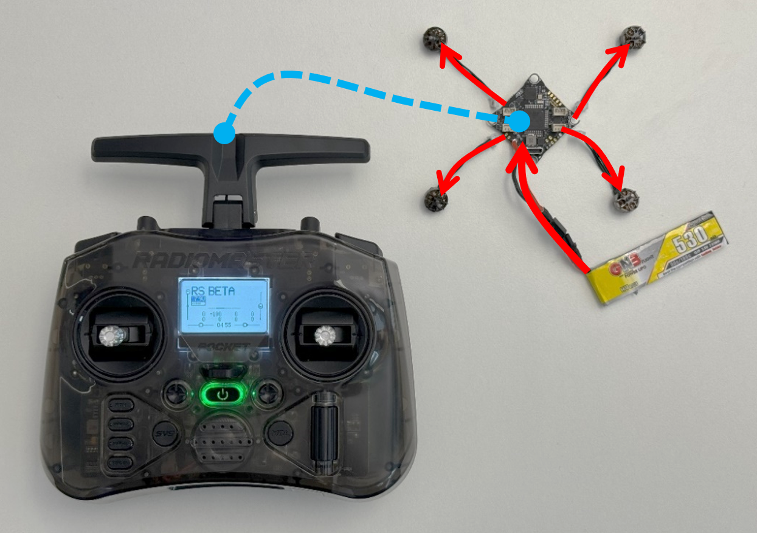
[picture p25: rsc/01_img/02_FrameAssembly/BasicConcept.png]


## Akku laden

Als allererstes werden wir die Akkus laden, damit sie mit Sicherheit voll sind, sobald es an den ersten Flug der Drohne geht.

**Wichtig:** Lies bitte unbedingt zuerst die Sicherheitshinweise zu Akkus bevor du fortfährst. Klicke dazu [hier](/docs/09_Safety.md#sicherer-umgang-mit-lipo-akkus).

Die Stromstärke stellst du mit mehrmaligem kurzem Drücken des *Current Set* - Buttons (1) ein. Die Spannung stellst du mit mehrmaligem kurzem Drücken des *Voltage Set* – Buttons (2) ein. 

Wenn du die richtigen Werte für Stromstärke (4) und Spannung (6) eingestellt hast, kannst du das Laden durch **langes** Drücken des *Start/Stop*–Buttons (1) starten. Dadurch werden Stromstärke (4) und Spannung (6) rot hinterlegt und lassen sich jetzt auch erst wieder ändern, wenn du das Laden durch langes Drücken des *Start/Stop*–Buttons (1) unterbrichst.

Den/die Akkus kannst du jetzt einfach anstecken. Im Feld (7) sollte dann auch dessen aktuelle Spannung angezeigt werden. Ein roter blinkender Punkt auf der linken Seite signalisiert, dass er geladen wird.

Grundsätzlich ist das Ladegerät auch Hot-Plug-fähig, sprich du kannst jederzeit einen Akku an- oder abstecken. Es ist dennoch ratsam einen Akku nur dann an- oder abzustecken, wenn du dir auch sicher bist, dass du das möchtest.

Die Spannung (5) ist lediglich die Eingangsspannung des Netzteils. Diese kann auch einen anderen Wert haben als auf dem Bild, lass dich davon nicht verwirren.

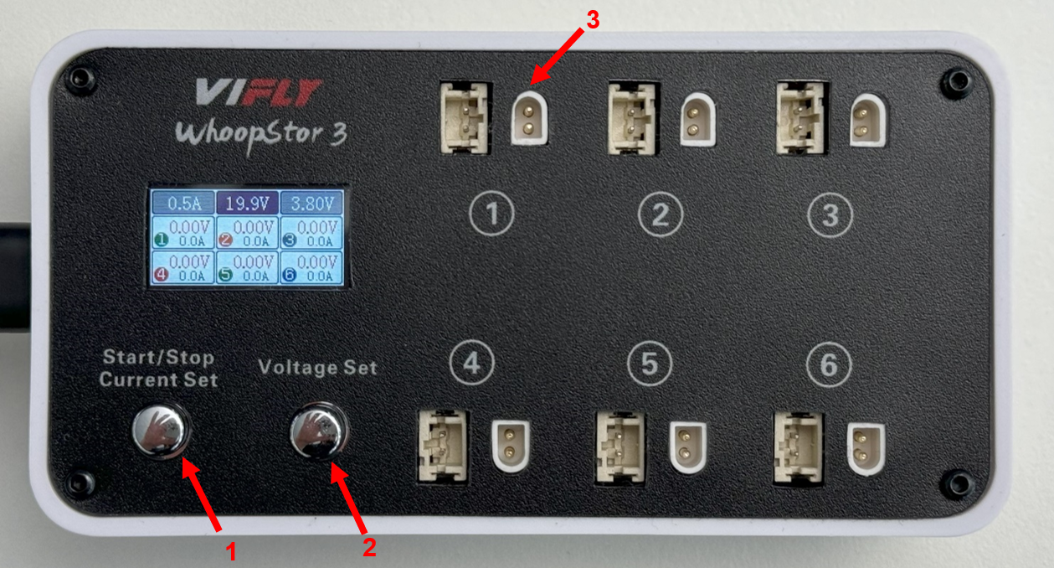
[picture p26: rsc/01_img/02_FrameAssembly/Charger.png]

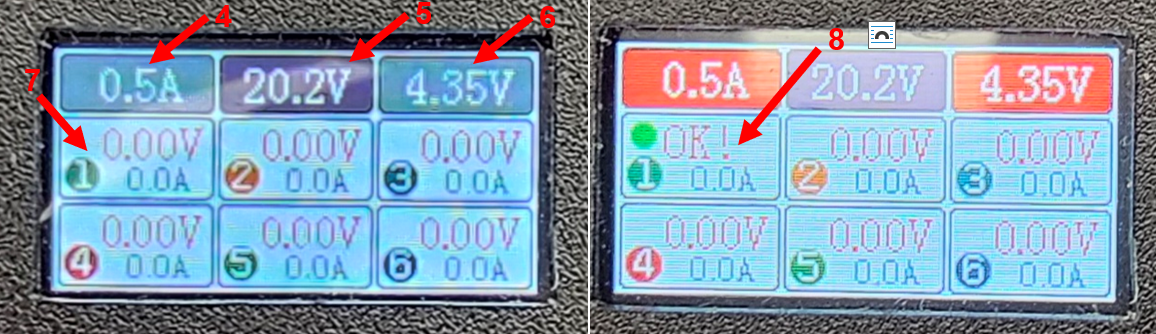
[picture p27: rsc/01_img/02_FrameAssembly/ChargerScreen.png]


Wenn der Akku fertig geladen ist, sprich die Spannung des Akkus (7) gleich der Zielspannung (6) ist, dann stoppt das Ladegerät für diesen Akku automatisch und zeigt *OK!* (8) an.

## 3D-Druck

Einige Teile der Drohne werden aus Plastik gedruckt. Dies sind die farbigen Markierungen des Rahmens, der Standfuß und die Deckplatte. Wenn du vor Ort in der Garage das Projekt machst sind die Teile bereits vorgedruckt und du musst dich mit der Thematik nicht weiter beschäftigen.

Wenn du die Teile bei dir zuhause mit einem einfarbigen Drucker druckst, findest du [hier](https://download-directory.github.io/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) die STEP, STL, 3mf und G-Code Dateien. Wenn dein Drucker mehrere Materialien gleichzeitig drucken kann (z.B: Bambulab mit AMS) findest du [hier](https://download-directory.github.io/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) STEP und STL-Dateien. 

Mit den STEP-Dateien kannst du in einem CAD-Programm deiner Wahl Änderungen an den Teilen vornehmen. Die STL-Dateien kannst du in einen Slicer deiner Wahl laden und für deinen eigenen Drucker G-Codes erstellen. Als Besonderheit findest du auch 3mf Projekt-Dateien für den PrusaSlicer. Diese sind nach dem Muster *ZuDruckendeTeile_Material_Drucker.3mf* benannt. Nach dem gleichen Muster sind auch fertig geslicte Dateien für den Prusa MK3s mit der Endung .gcode verfügbar. Achte stets darauf nur Dateien zu Drucken, die für den 3D-Drucker und das geladene Material gedacht sind, ansonsten kann es zu Schäden an dem Drucker kommen.

Geeignete Materialien für Standfuß und Deckplatte sind **PETG oder ABS**. Für die Markierungen solltest du **TPU** verwenden, falls dein Drucker dies drucken kann. Ansonsten verwende ebenfalls PETG oder ABS. Die Farben für die zwei Markierungen sollten farblich gut unterscheidbar sein, da sie die als Orientierung für die Ausrichtung der Drohne dienen.

## Kleben der Markierungen und des Standfußes

Als allererstes werden wir der Drohne ein *Vorne* und ein *Hinten* geben.

>Wie du auf dem Deckblatt mit der fertigen Drohne vielleicht schon erkannt hast, ist es ohne die farblichen Markierungen schwierig, vorne von hinten oder links von rechts zu unterscheiden. Ohne diese Referenzpunkte zur Orientierung, hättest du es später sehr schwer, die Drohne zu steuern.

Da der Kleber für den Standfuß etwa 20min braucht, um einigermaßen fest zu werden, starten wir mit den Klebeteilen. Bis der Kleber angetrocknet ist, werden wir uns dann mit der Fernbedienung beschäftigen.

Allgemein solltest du alle Klebeflächen einmal abwischen, **bevor** du Kleber oder Klebeband anbringst, um Fettrückstände und Verunreinigungen zu entfernen.

Zuerst bringen wir die **blaue** Markierung auf einer beliebigen Seite, die senkrecht zur im Bild eingezeichneten Mittelachse (1) liegt, an. Um die Achse zu finden, kannst du dich auch an der pfeilartigen Stelle im Rahmen (2) orientieren. Du nimmst also das doppelseitige Klebeband und klebst es so wie unten zu sehen, auf den Außenseiten des Rahmens an. Du kannst das Band an einem Stück anbringen oder in Einzelteilen, wie es dir lieber ist. Entferne die Schutzfolie des Klebebandes erst, wenn es an Ort und Stelle ist und du die Markierung ankleben willst. Das vereinfacht das initiale Ankleben deutlich.

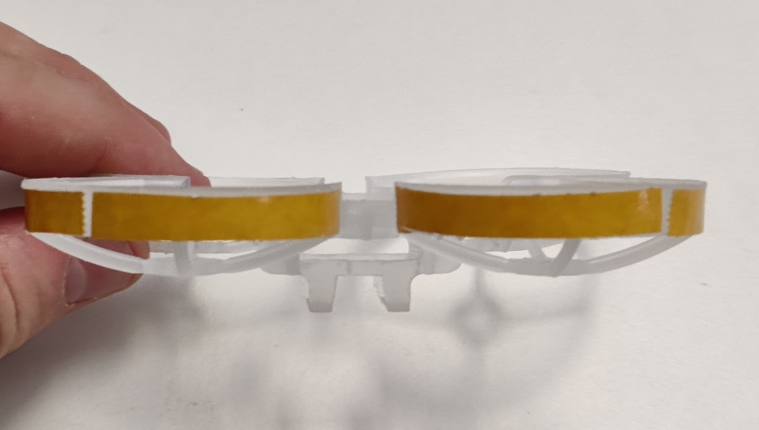
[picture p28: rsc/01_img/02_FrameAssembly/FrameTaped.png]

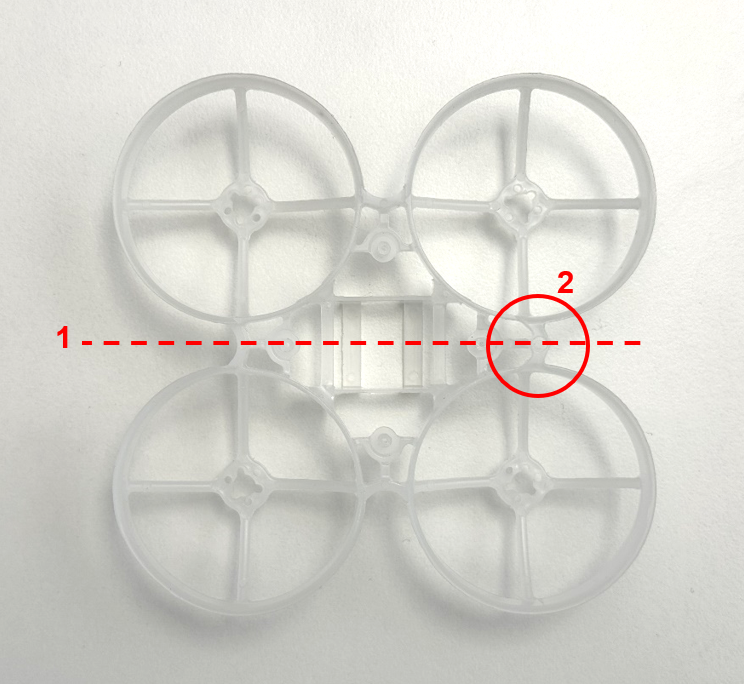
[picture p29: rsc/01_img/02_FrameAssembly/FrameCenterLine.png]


Drücke dann die Markierung wie auf dem Foto an den Rahmen an. Anschließend machst du das Gleiche mit der **roten** Markierung auf der gegenüberliegenden Seite der Drohne. 

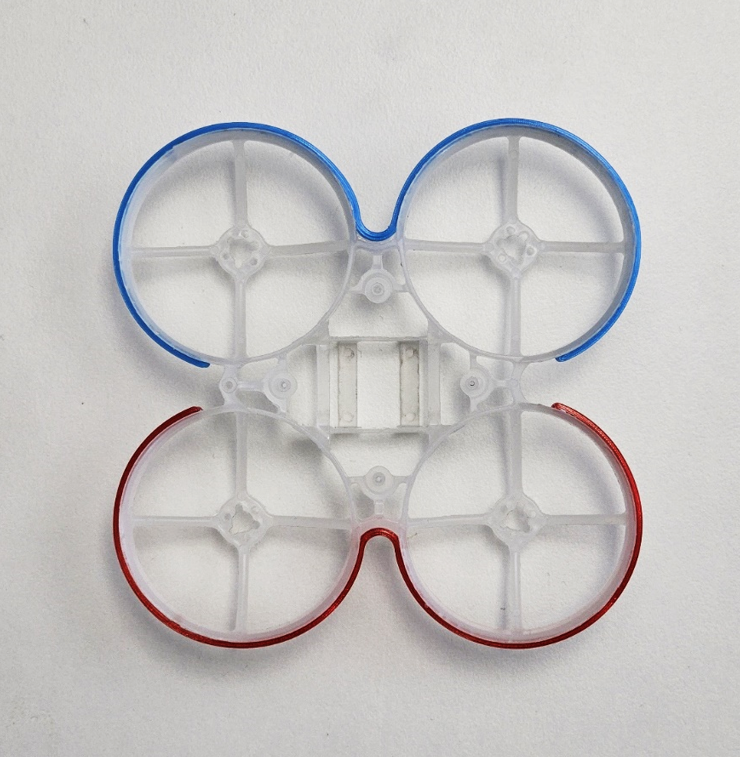
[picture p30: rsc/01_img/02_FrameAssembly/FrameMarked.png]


Nun fehlt nur noch der Standfuß. Dieser besteht anfangs noch aus zwei Teilen.

Uhu Extreme ist ziemlich gutmütig, was die Verarbeitungszeit angeht, das heißt er wird nicht sofort fest und ist daher nicht so gefährlich im Umgang. **Achte dennoch** darauf, dass deine Finger sauber bleiben und kein Kleber auf den Boden o.ä. tropft. Lege dir **vor** der Verarbeitung ein Papiertuch bereit, um eventuelle Tropfen sofort wegwischen zu können und wasche dir **sofort** die Hände, sollten sie doch schmutzig werden.

Trage also etwas Uhu Extrem Kleber auf beide Klebeflächen auf und presse das Unterteil des Standfußes an das Oberteil. Am besten du drückst die zwei Teile dabei zwischen Daumen und Zeigefinger (s. Foto).

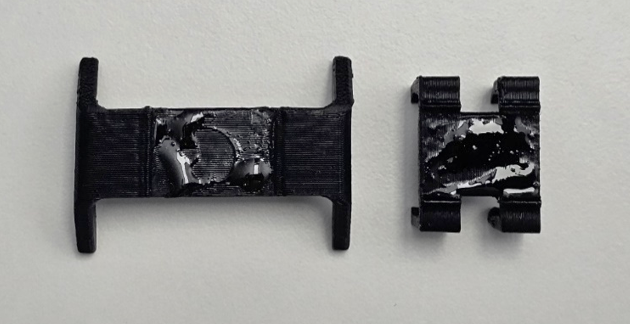
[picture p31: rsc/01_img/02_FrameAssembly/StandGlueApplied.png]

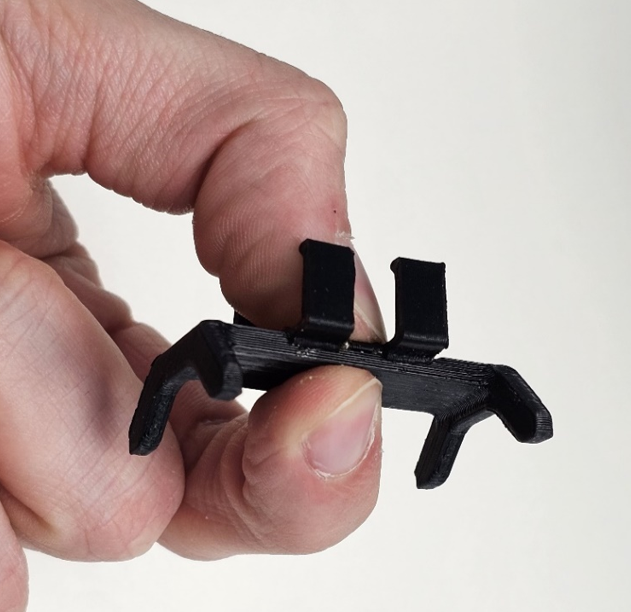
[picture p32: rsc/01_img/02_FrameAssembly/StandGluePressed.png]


Ab jetzt legst du Drohne und den Standfuß in eine Ecke, wo die Gefahr möglichst gering ist, dass die angeklebten Teile in den nächsten 20 Minuten verrutschen.

## [Klicke hier, um zurück zur Übersicht der Kapitel zu kommen!](/README.md#kapitel)

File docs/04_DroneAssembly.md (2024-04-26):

# Zusammenbau Drohne


Nachdem du nun die Fernbedienung und das Übertragungsmodul eingerichtet hast, geht es jetzt an den Zusammenbau der eigentlichen Drohne.

Inzwischen sind wahrscheinlich mehr als 20min vergangen, daher kannst du die Drohne nun aus ihrer Ecke nehmen und wir beginnen den Aufbau.

## Motoren

Nimm die vier Motoren zur Hand. Wir werden diese am Rahmen anbringen. Dazu müssen wir Schraubensicherung verwenden. Der Einfachheit halber kannst du die Motoren aber schon mal **locker** mit 2 der 3 Schrauben anbringen und erst anschließend bringen wir auf jede Schraube die Schraubensicherung auf (die Schrauben also noch **nicht ganz** anziehen). Achte dabei darauf, dass die Kabel in Richtung der Mittelachse zeigen. 

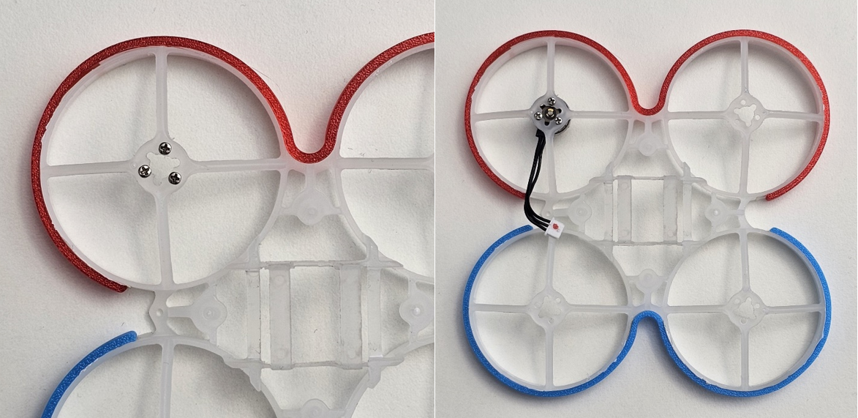
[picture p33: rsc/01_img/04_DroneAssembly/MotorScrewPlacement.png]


Da der Motor jetzt mit den zwei Schrauben an Ort und Stelle bleibt, trage auf die dritte Schraube einen kleinen Tropfen Schraubensicherung auf und ziehe sie vorsichtig fest. Fest bedeutet dabei wirklich nur, bis die Schraube ganz drin ist. Wende also nicht viel Kraft auf, da sie sonst eventuell abreißen könnte.

**Tipp:** Wenn du statt der ganzen Hand nur zwei Finger zum Drehen des Schraubenziehers verwendest, wendest du automatisch weniger Kraft an. 

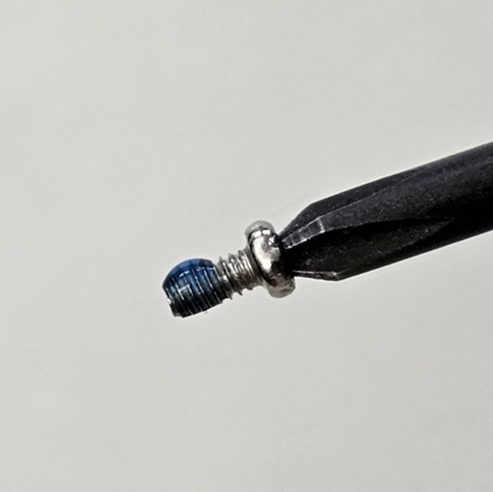
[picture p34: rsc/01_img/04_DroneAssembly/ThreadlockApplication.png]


>Schraubensicherung benötigen wir deswegen, weil sich durch die Vibrationen und die vielen Beschleunigungsmomente des Motors die Schraube langsam Stück für Stück wieder lösen könnte. Ähnlich wie sich eine Schleife am Schuh irgendwann lösen kann, ohne dass du tatsächlich an einem Ende gezogen hast. Die Schraubensicherung verhindert das, indem sie die Schraube ähnlich wie ein Kleber festhält, sodass mehr Kraft notwendig ist, um sie zu lösen.

Wiederhole das gleiche mit den anderen 2 Schrauben, indem du sie herausdrehst und nach dem Aufbringen der Schraubensicherung festziehst.

Den ganzen Prozess wiederholst du nochmal für die drei anderen Motoren. Achte auch dort bitte auf die richtige Orientierung der Kabel. Deine Drohne sollte jetzt folgendermaßen aussehen. 

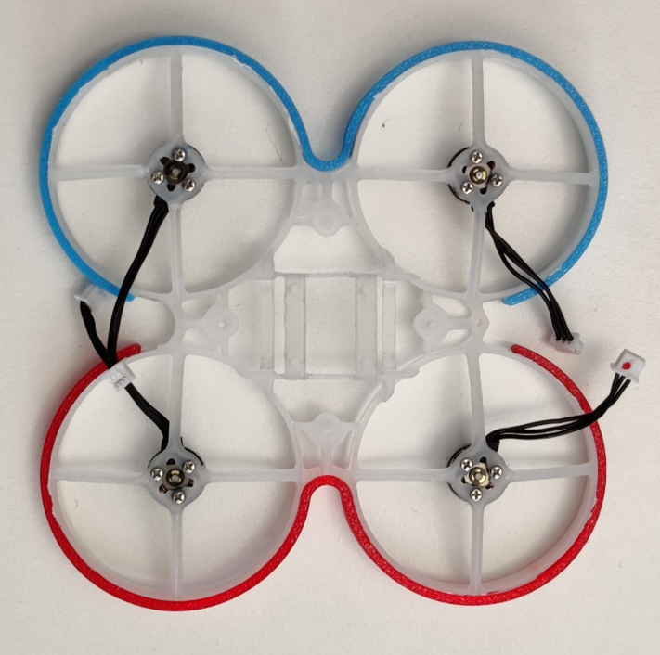
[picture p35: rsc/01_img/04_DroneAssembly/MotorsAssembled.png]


## Flight Controller

Zuerst musst du kontrollieren ob an dem Flight Controller der richtige Stecker angelötet ist. Dieser heißt A30 (1) und eignet sich am besten für kleine Drohnen. Alternativ kannst du für den Flight Controller auch BT2.0 (2) Stecker verwenden. Am Ende der Anleitung findest du [Links](/docs/08_Links.md#drohne) zu den verwendeten Steckern. Diese sind als Pigtail vorgefertigt – Stecker sind bereits mit Kabeln vorbereitet – und die Verwendung spart dir viel Arbeit.

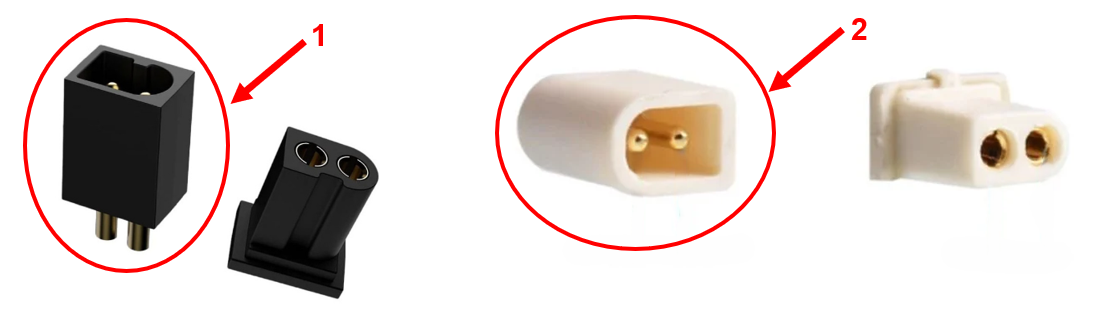
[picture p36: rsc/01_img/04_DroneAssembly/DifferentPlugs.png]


Sollte der Stecker noch nicht vorhanden sein so musst du diesen erst an den Flight Controller anlöten. Wenn du noch keine Erfahrung mit Löten hast, so findest du [hier](https://www.conrad.de/de/ratgeber/handwerk/richtig-loeten-lernen.html) ein gutes Tutorial. Alternativ kannst du gerne zu uns in die Garage kommen und dich mit professionellem Equipment in das Löten einarbeiten. 

Achte beim Löten des Steckers auf die **korrekte Polung**, da ansonsten es zu einer Beschädigung des Flight Controllers kommt, sobald du die Batterie ansteckst. Ebenfalls müssen die Kabel auf der Seite des Micro-USB Ports angelötet werden, da es ansonsten zu Problemen beim Verbau kommt.

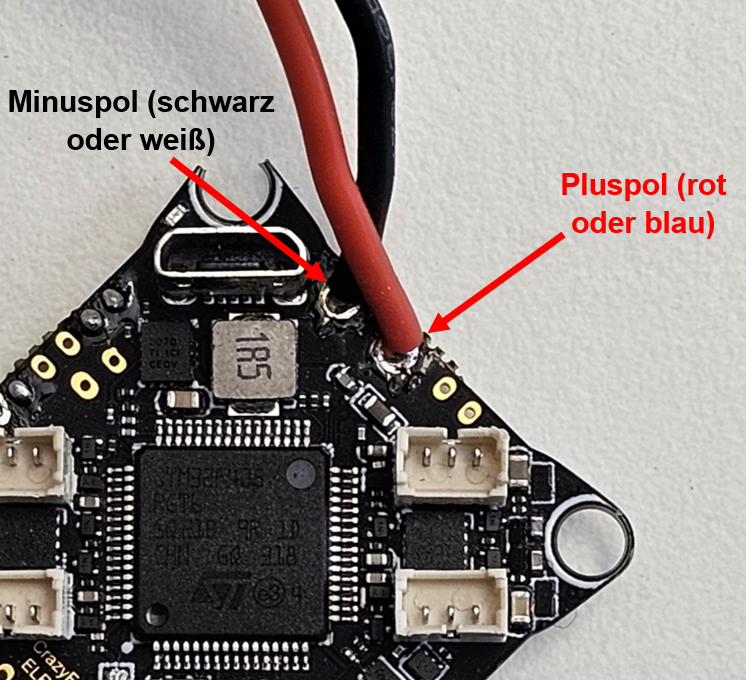
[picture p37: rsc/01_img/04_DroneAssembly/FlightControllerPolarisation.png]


Als nächstes werden wir das Herz der Drohne, den Flight Controller, montieren. Dieser braucht zunächst seine Standfüße, die du am besten mit einer Pinzette durch die Löcher ziehst. Das ist etwas tricky, lass dich nicht entmutigen, mit ein wenig Übung wirst du es schaffen. Achte darauf mit der Pinzette nicht abzurutschen und dabei die elektrischen Komponenten auf dem Board zu beschädigen. Achte außerdem auch auf die Orientierung, sodass die **lange Seite der Gummifüße auf derselben Seite wie der USB-Anschluss des Flight Controllers ist**. 

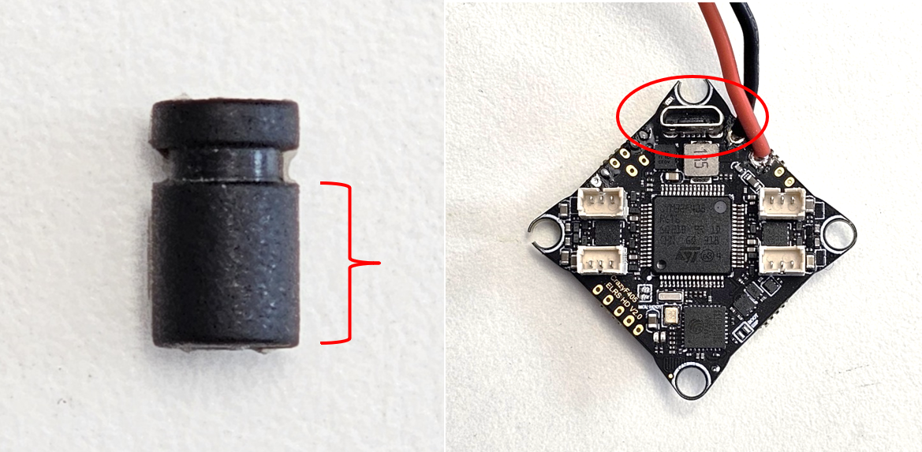
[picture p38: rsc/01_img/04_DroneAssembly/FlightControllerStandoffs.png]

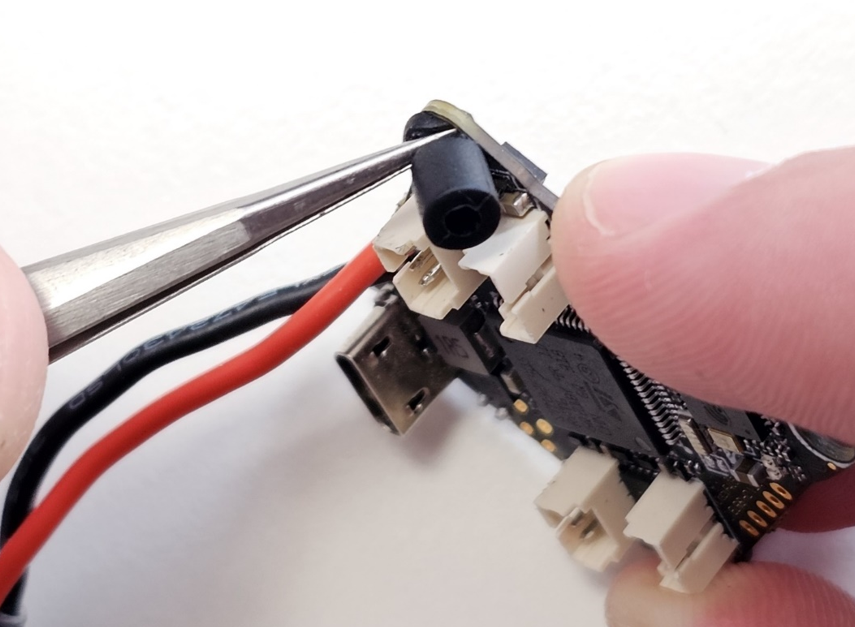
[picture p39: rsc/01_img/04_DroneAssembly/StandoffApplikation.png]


Der gesamte Flight Controller mit den Gummifüßen soll nun auf den Rahmen gesetzt werden. Die Orientierung soll so wie auf dem Bild sein, sodass der USB-Anschluss nach unten zeigt und auf der hinteren Seite der Drohne ist (rote Markierung). Da die Anschlüsse der Motoren nach der Montage des Flight Controllers nicht mehr zugänglich sind, müssen diese **vor** der Montage eingesteckt werden. Die Stecker haben auf einer Seite eine Nase, die nur in einer Richtung passt. Sieh sie dir genau an und dann steck sie ein. Die Kabel müssen in etwa so geführt sein wie auf dem Bild, damit später keine Gefahr besteht, dass sie sich in den Propellern verfangen. Jetzt kannst du den Flight Controller auf die Montagepunkte im Rahmen senken. Es sollte aktuell so aussehen (Überprüfe insbesondere auch die Kabelverläufe):

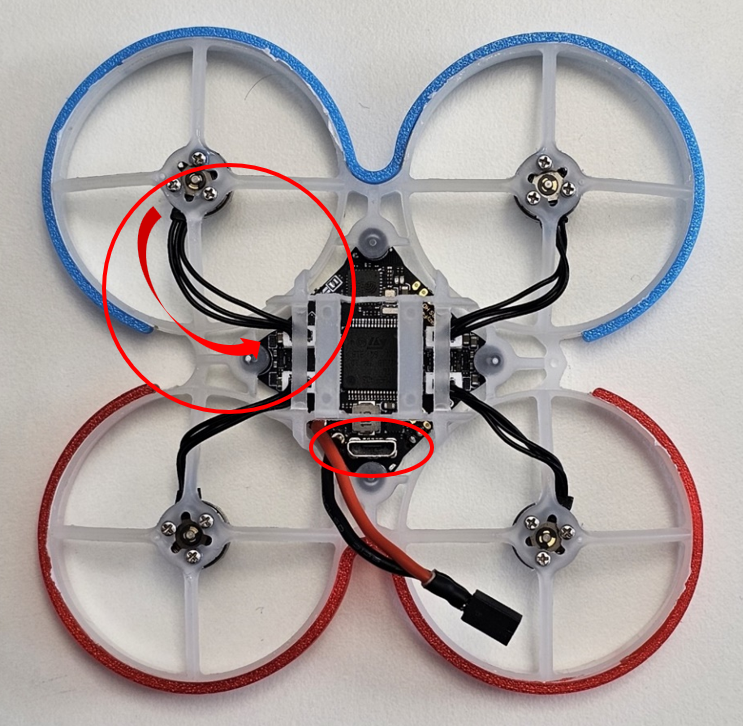
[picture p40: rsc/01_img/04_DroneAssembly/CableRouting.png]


Obendrauf kommt dann nur noch die schwarze Abdeckplatte mit R/S-Logo, achte auch bei ihr darauf, dass die Schrift in Flugrichtung „vorne“ zeigt (also in Richtung blaue Markierung). Befestigt wird alles mit den 4 noch verbleibenden Schrauben. Wie bei den Motorschrauben soll wieder nur so fest angezogen werden, dass die Schraube am Anschlag ist, damit sie nicht abreißt. 

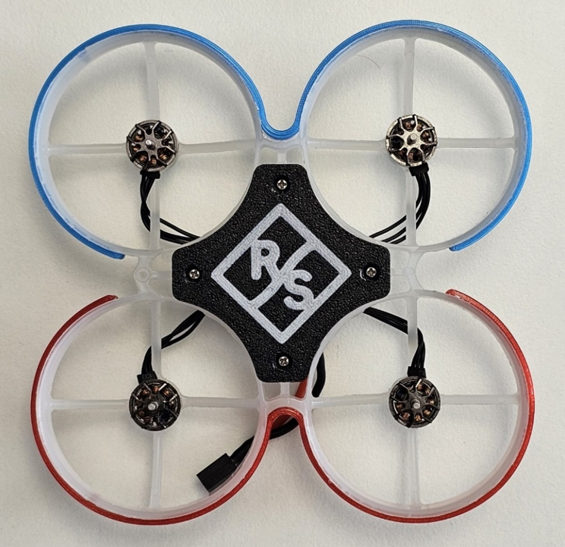
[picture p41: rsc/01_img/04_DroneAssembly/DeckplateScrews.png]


## Hinweis

Die wichtigsten Bauteile sind jetzt schon zusammengebaut, es fehlt also nicht mehr viel und die Drohne ist technisch gesehen flugbereit. Als erstes fallen dir bestimmt die noch fehlenden Propeller auf und natürlich braucht deine Drohne auch noch einen Akku. Die Anleitung zu deren Montage folgt hier auch gleich. Bitte lies aber unbedingt **zuerst** die [Sicherheitshinweise](/docs/09_Safety.md).

## Propeller

Es gibt für jeden Propeller eine Drehrichtung und auf der Drohne gibt es für jeden Motor eine Drehrichtung. Diese Richtungen müssen übereinstimmen.

>Die Drehrichtungen sind deswegen so wichtig, weil sich die Drohne später während des Fluges mit Hilfe verschiedener Drehzahlen zwischen den einzelnen Motoren dreht. Wenn alle Motoren in die gleiche Richtung drehen würden, dann würde sich die Drohne ständig drehen, ähnlich wie ein Helikopter, bei dem der hintere Rotor ausgefallen ist. Wenn nun zwei Motoren in die eine und zwei Motoren in die andere Richtung drehen, dann heben sich diese sogenannten Drehmomente gegenseitig auf und die Drohne steht still in der Luft. Gleichzeitig erhält man so eine einfache Möglichkeit die Drohne zu steuern. Indem man die Drehzahl der Motoren nur ein wenig anpasst dreht sie sich schon, weil insgesamt mehr Moment nach links, als nach rechts besteht oder eben umgekehrt.

Am einfachsten ist, du orientierst dich am untenstehenden Bild. Es ist sehr wichtig, dass die Richtungen stimmen, nimm dir also Zeit und prüfe genau. Die Drehrichtung der Propeller kannst du an der sogenannten leading edge, also an der führenden Kante des Propellers (in <code style="color : Orangered">Rot</code> eingezeichnet) erkennen.

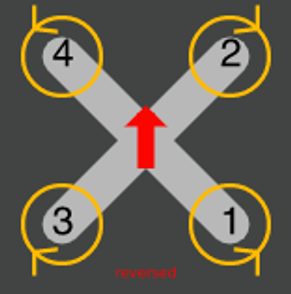
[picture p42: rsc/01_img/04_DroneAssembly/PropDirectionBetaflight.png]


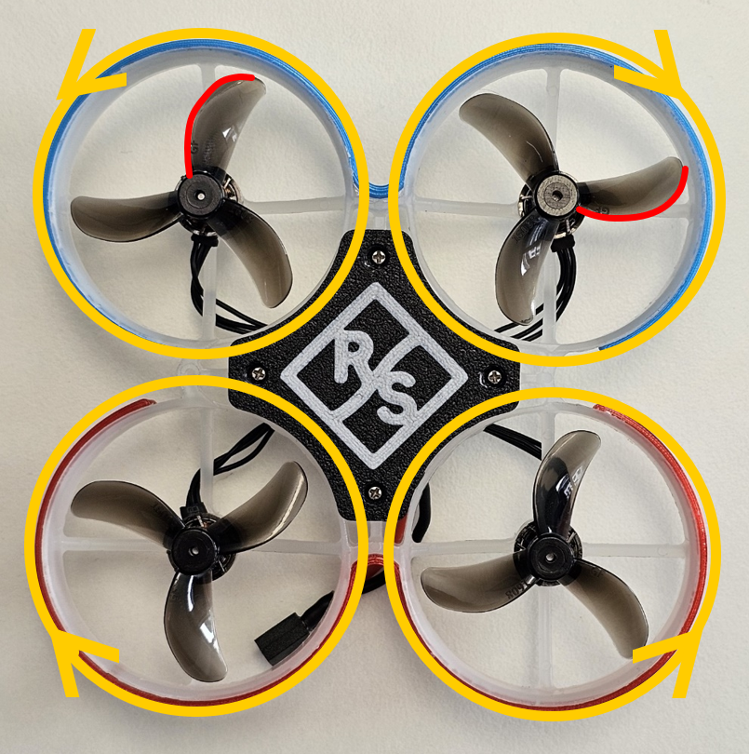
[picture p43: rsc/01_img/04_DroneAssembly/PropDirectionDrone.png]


Wenn du dir sicher bist, welcher Propeller wohin kommt, dann bleibt nur noch ihn aufzustecken. Dazu musst du nichts weiter machen, als ihn vorsichtig aufzustecken. Halte gleichzeitig von hinten dagegen, damit sich dabei nicht der Rahmen verbiegt. Es kann etwas Kraft benötigen bis der Propeller ganz auf der Achse steckt. Es gilt der Grundsatz: so wenig Kraft wie möglich, aber so viel wie nötig.

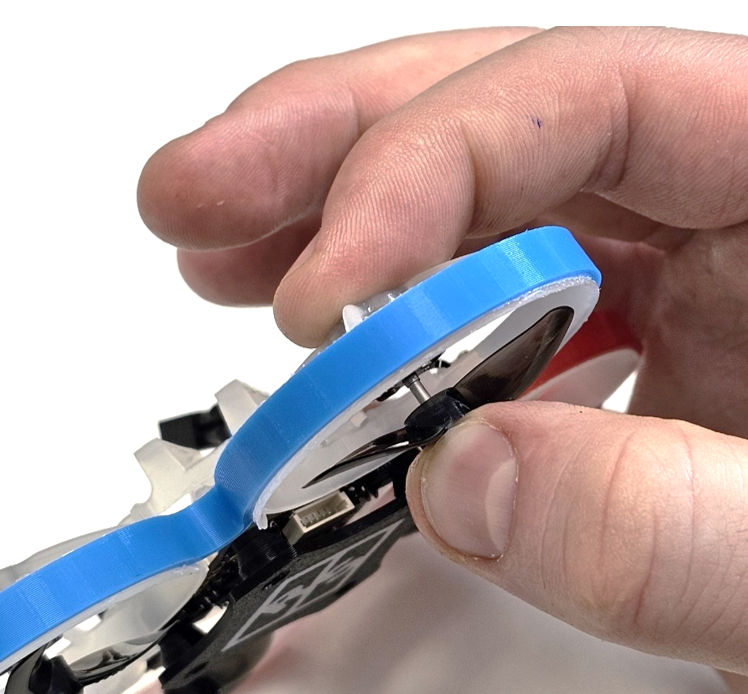
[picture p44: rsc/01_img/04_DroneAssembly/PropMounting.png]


## Standfuß montieren

Nun befestigst du den zusammengeklebten Standfuß an dem Rahmen der Drohne. Hierfür clipst du diesen, wie auf dem Bild ersichtlich um den Rahmen. Es ist möglich, dass du dafür den Rahmen etwas zusammendrücken musst. Übe dabei allerdings nicht zu viel Kraft aus.

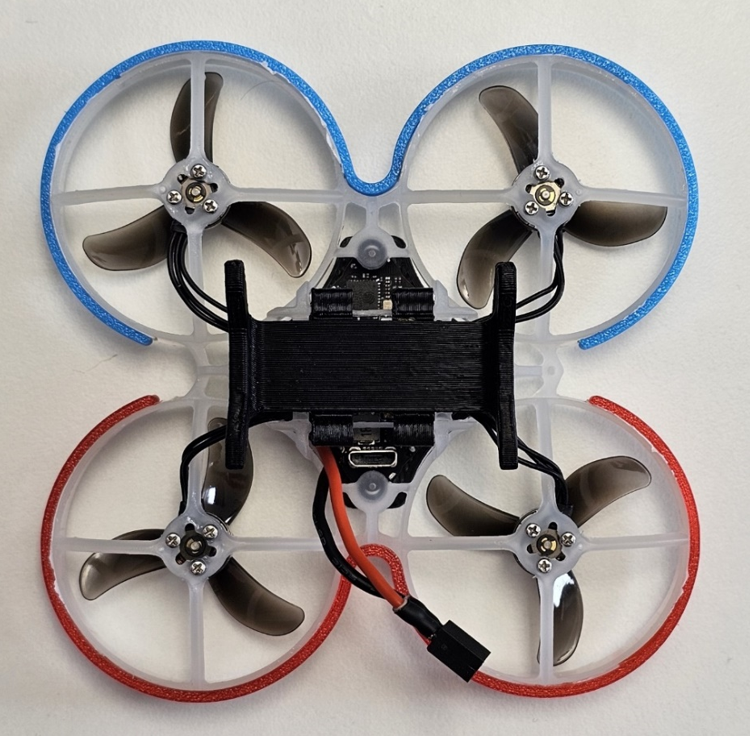
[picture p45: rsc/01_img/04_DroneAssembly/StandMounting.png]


## Akku einbauen

Zu guter Letzt musst du vor Benutzung der Drohne nur noch den Akku in seine Halterung einführen. Stecke den Akku aber noch nicht an bzw. vom Ladegerät ab, bis du bei [Konfiguration Motorsteuerung](/docs/05_FlightControllerSetup.md#konfiguration-motorsteuerung) angekommen bist.

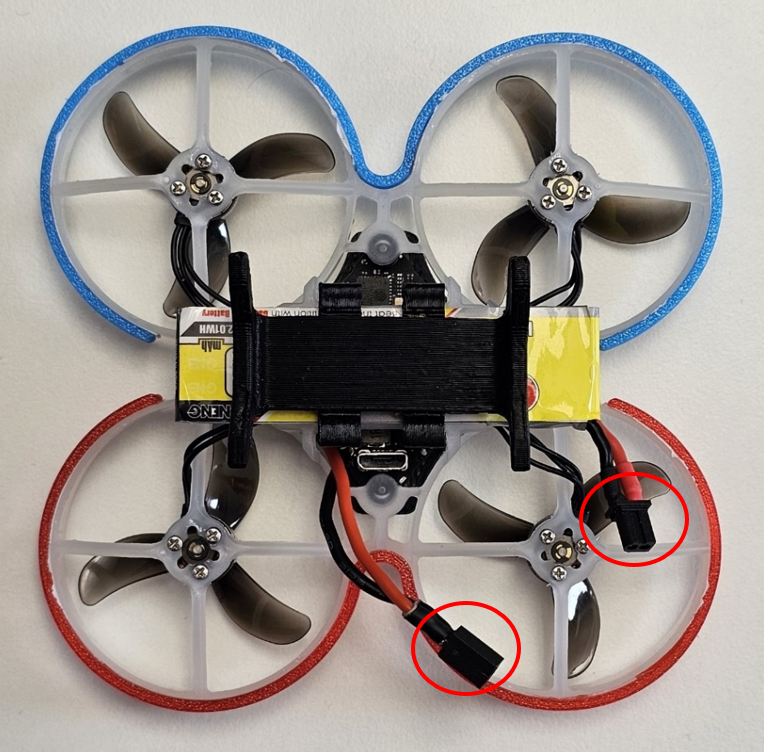
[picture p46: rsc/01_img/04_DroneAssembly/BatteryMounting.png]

  
## [Klicke hier, um zurück zur Übersicht der Kapitel zu kommen!](/README.md#kapitel)

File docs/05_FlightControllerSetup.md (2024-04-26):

# Inhalt


1. [Einrichten Flight-Controller](#einrichten-flight-controller)

2. [Konfiguration Motorsteuerung](#konfiguration-motorsteuerung)

3. [Konfiguration Empfangsmodul](#konfiguration-empfangsmodul)

# Einrichten Flight-Controller


Damit die Drohne fliegen kann muss nicht nur die Hardware korrekt zusammengebaut sein, sondern auch die Software richtig konfiguriert sein. Einen Großteil, die Flugsteuerung im Flight Controller, werden wir in diesem Kapitel erledigen.

Wir starten damit die Firmware auf den Controller zu flashen.

> Firmware kannst du dir im Grunde vorstellen wie das Betriebssystem auf deinem PC/Laptop zu Hause. Erst dadurch kannst du mit der Hardware interagieren und sie das machen lassen, was du möchtest. Erst dadurch kannst du Einstellungen vornehmen, Programme ausführen, Internetseiten öffnen usw. Auf dem Flight Controller läuft nur eben kein Windows, Android oder iOS, sondern ein ganz spezielles für diesen Zweck entwickeltes Betriebssystem namens _Betaflight_. Dieses Betriebssystem müssen wir nun zu anfangs installieren, was man allgemein auch „flashen“ nennt.

**Wichtig:** Immer wenn du den Flight Controller länger als ein paar Sekunden mit dem PC verbindest, richte einen Lüfter auf ihn. Gerade während des Flashens kann er sehr heiß werden. Ohne ein wenig Kühlung riskiert man im besten Fall ein Abstürzen des Controllers, was insbesondere wenn man Einstellungen noch nicht gesichert hat, sehr ärgerlich sein kann. Im schlimmsten Fall kann es bei manchen Flight Controllern sogar zu Defekten führen.

Um Betaflight installieren zu können, müssen wir den Controller zuerst in einen speziellen Modus versetzen, der diese Art von Zugriff ermöglicht. Nimm einen kleinen Flachkopfschraubenzieher zur Hand und halte ihn wie auf dem Bild auf die markierten Kontakte (1) auf dem Flight Controller. Während du immer noch die zwei Kontakte mit dem Schraubenzieher verbunden hältst, verbinde den Controller mit dem USB-Kabel an den PC.  Möglicherweise ist es einfacher das mit einer zweiten Person gemeinsam zu machen, sodass eine nur die Kontakte mit dem Schraubenzieher verbindet und die andere nur das Kabel ansteckt. Hast du alles richtig gemacht, dann blinkt nur die rote LED (2) auf der gegenüberliegenden Seite des USB-Anschlusses. Falls etwas schiefgelaufen ist, dann blinken sowohl die etwas kleinere grüne LED als auch die hellere rote LED abwechselnd. In diesem Fall wiederholst du den Prozess einfach (Kabel nochmal abstecken und dann wieder anstecken). Achte vor allem darauf, dass der Schraubenzieher tatsächlich die zwei Kontaktstellen verbindet.

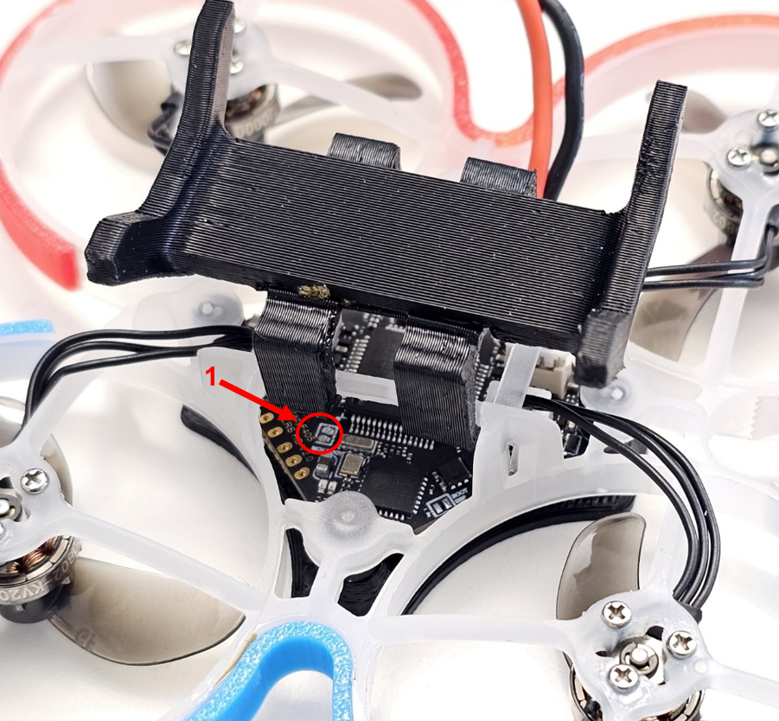
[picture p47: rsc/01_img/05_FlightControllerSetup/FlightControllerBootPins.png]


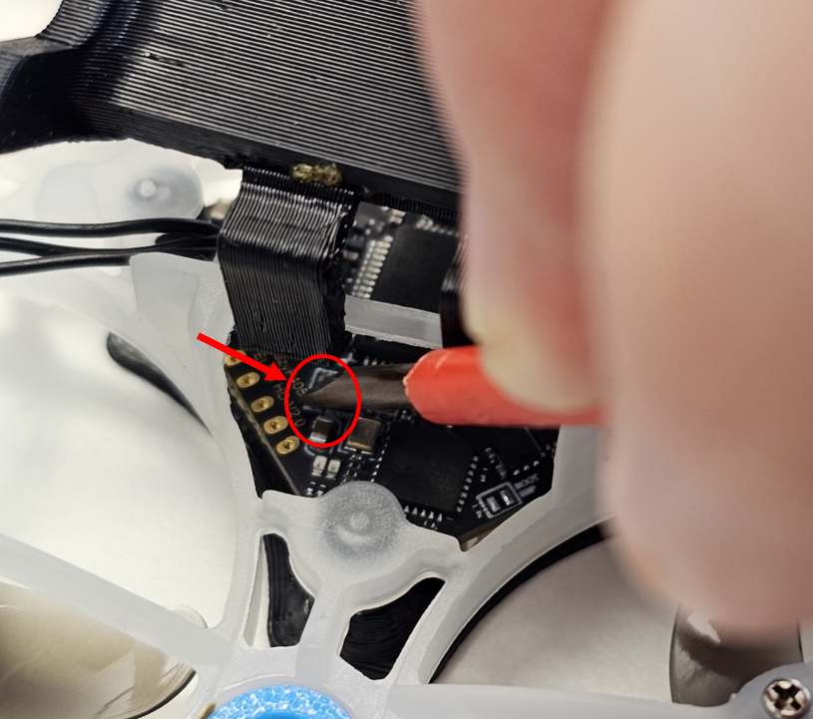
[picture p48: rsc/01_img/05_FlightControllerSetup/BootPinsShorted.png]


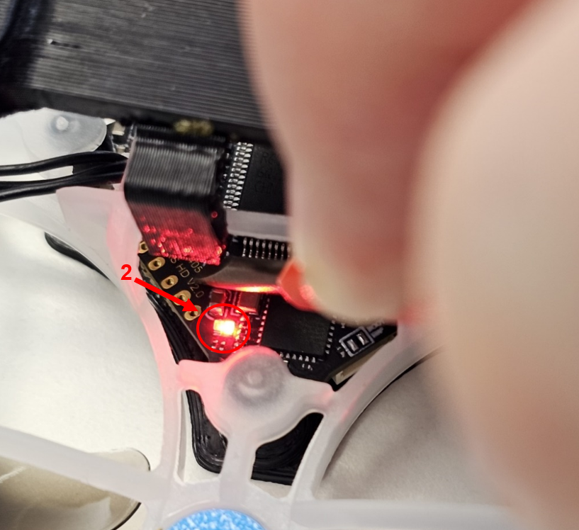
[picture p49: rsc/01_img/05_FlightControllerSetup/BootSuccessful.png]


Sobald also ausschließlich die rote LED blinkt, öffne auf dem PC das Programm _Betaflight Configurator_. Du solltest es wie in [Installation Software und Treiber](/docs/01_Materials.md#installation-betaflight-konfigurator) beschrieben bereits installiert haben. Falls nicht, solltest du das jetzt nachholen. Die Startseite sollte in etwa wie auf dem Bild aussehen. Achte darauf, dass weder der _ExpressLRS Configurator_ noch der _ESC Configurator_ (aus einem späteren Kapitel) geöffnet sind, während du im _Betaflight Configurator_ arbeitest.

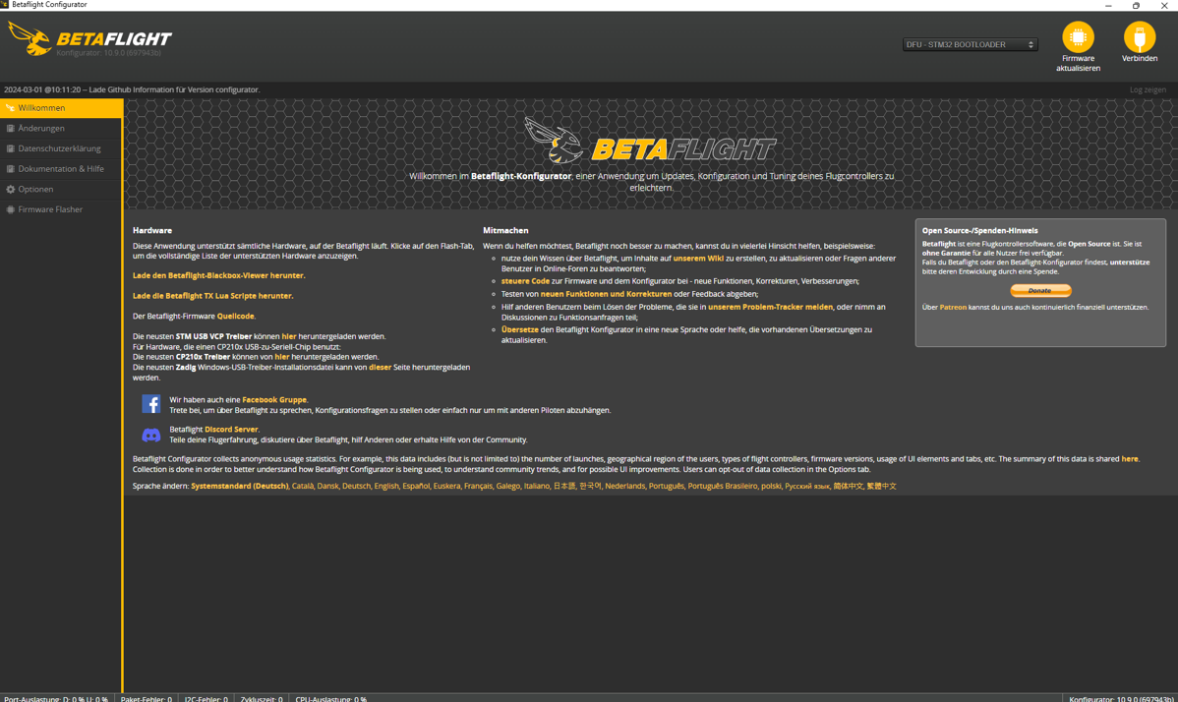
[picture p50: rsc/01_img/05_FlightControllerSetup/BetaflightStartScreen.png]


>_Betaflight Configurator_ ist eine Software, mit der die Firmware auf den Flight Controller geflashed werden kann und anschließend dann alle Einstellungen vorgenommen werden können, damit der Flight Controller genau das macht, was du möchtest. Der Zugriff erfolgt über die USB-Verbindung. Um also Einstellungen zu tätigen, muss der Flight Controller später wieder per USB-Kabel verbunden werden.

Wähle nun links den Reiter _Firmware Flasher_ (1). Im Einstellungsfeld (2) wählst du BetaflightF4, **in der Version 4.4.3** und aktivierst **Chip vollständig löschen**. Dann sollte das Fenster so aussehen wie auf dem Bild. Wichtig ist, dass oben rechts DFU – STM32 Bootloader angezeigt wird. Das bestätigt, dass der Flight Controller im richtigen Modus ist und damit auch, dass du davor beim Verbinden der Kontakte alles richtig gemacht hast. Eine mögliche Fehlerquelle können auch wieder fehlende Treiber sein. In diesem Fall insbesondere der STM32-Treiber. Halte dich an die Anleitung in [Installation Software und Treiber](/docs/01_Materials.md#installation-stm32-virtual-com-port-treiber), um das zu beheben. Achte außerdem darauf, dass alle anderen Programme geschlossen sind.

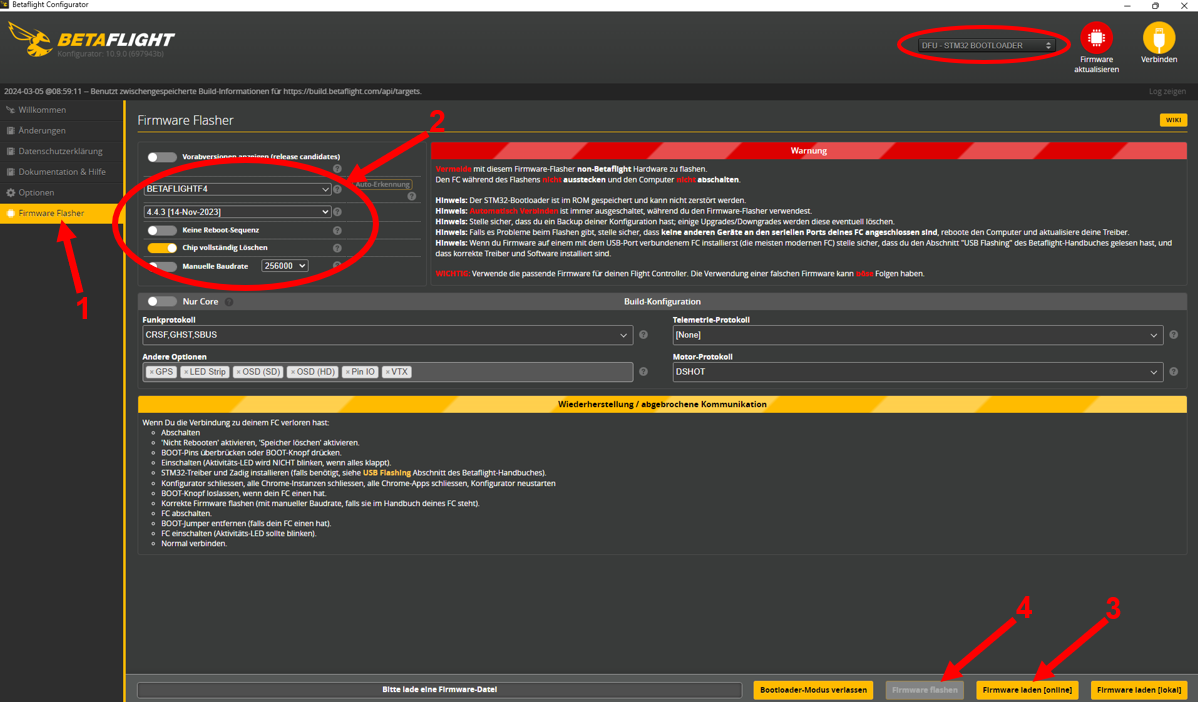
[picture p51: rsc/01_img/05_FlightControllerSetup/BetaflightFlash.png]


Jetzt kannst du die Firmware online laden (3). Sobald der Vorgang abgeschlossen ist, wird der Button _Firmware Flashen_ (4) auch gelb werden und du kannst auch ihn drücken. Dann beginnt das eigentliche Flashen. Es dauert ein paar Sekunden und wird quittiert mit einem grünen Balken und der Meldung Programmierung erfolgreich (5).

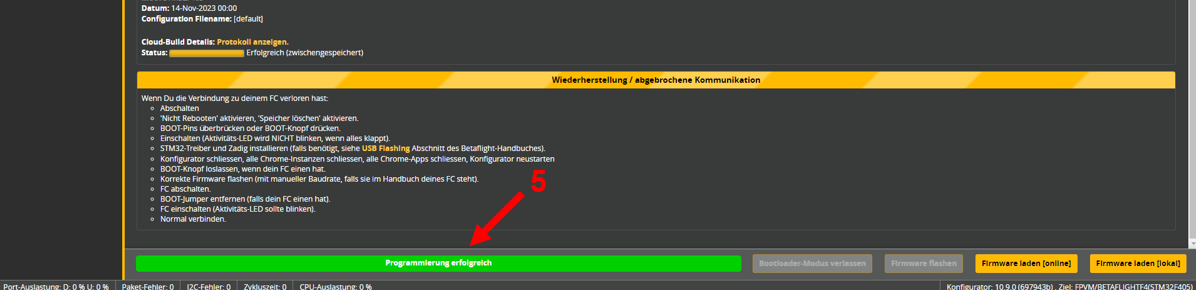
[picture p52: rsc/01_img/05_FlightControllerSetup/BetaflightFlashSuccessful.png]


Jetzt sollte oben rechts statt _DFU – STM32 Bootloader_ dann _COM3 – Betaflight STM32F405_ stehen (statt _COM3_ kann es an deinem PC möglicherweise auch eine andere Zahl als 3 sein). Drücke auf _Verbinden_ (7). Wahrscheinlich ploppt ein Fenster auf, in dem es um Standardeinstellungen geht. Dort musst du den Button _Benutzerdefinierte Standardeinstellungen_ anwenden drücken.

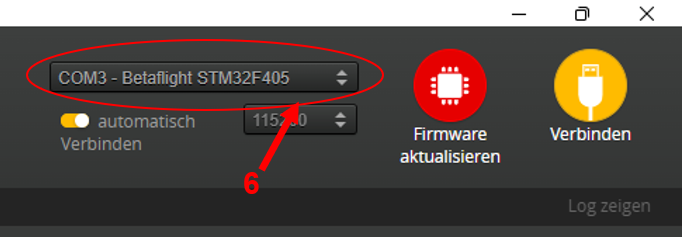
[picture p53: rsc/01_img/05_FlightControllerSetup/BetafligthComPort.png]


Du solltest jetzt in der Benutzeroberfläche sein, in der du so ziemlich alles einstellen kannst, was es gibt. Wenn du deine Drohne ein wenig in der Luft drehst und schwenkst, solltest du genau diese Bewegungen auch in der Anzeige (7) sehen können.

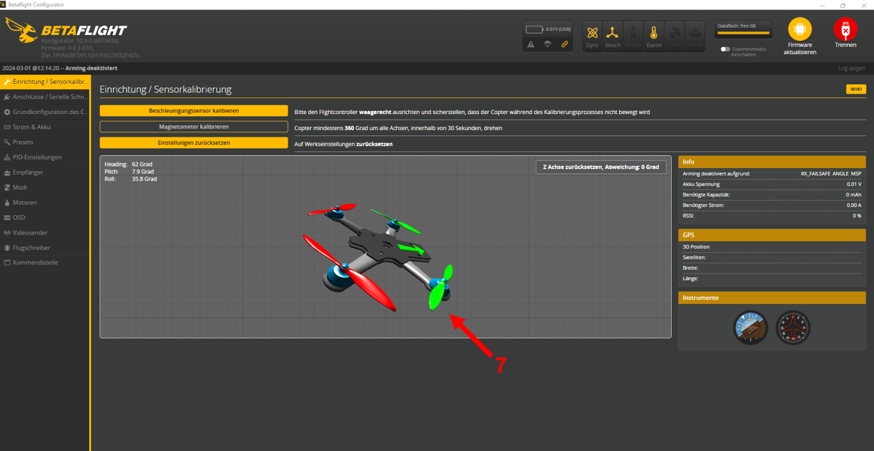
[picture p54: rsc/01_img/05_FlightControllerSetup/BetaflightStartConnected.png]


>Während wir bei normalen PCs und Laptops meistens über Bildschirme interagieren, an die direkt vom Rechner ein Videosignal gesendet wird, ist das beim Flight Controller etwas anders. Er ist nur per USB an den PC angebunden und wir können aber die speziell dafür entwickelte Software _Betaflight Configurator_ daran Einstellungen in einer grafischen Benutzeroberfläche vornehmen. Im Grunde fungiert der PC nur als Übermittler.

Im aktuellen Zustand lässt sich mit der Drohne aber noch nicht viel anfangen. Sie hat weder eine Verbindung zur Fernbedienung, noch weiß sie, wie sie auf verschiedene Befehle der Fernbedienung reagieren soll. Auch weiß die Drohne noch nicht, was sie überhaupt für Komponenten besitzt und wie sie diese intern ansteuern muss.

Für die allermeisten dieser Einstellung gibt es schon ein gutes Preset (bereits davor abgespeicherte Konfiguration), das die meiste Arbeit für dich erledigt. Du findest es im Reiter _Presets_ (8). Die Kachel _ExpressLRS 150Hz_ (9) sollte ganz oben links zu sehen sein. Falls sie nicht zu sehen ist, kannst du einfach im Suchfeld (10) danach suchen, indem du dort _ExpressLRS_ eingibst.

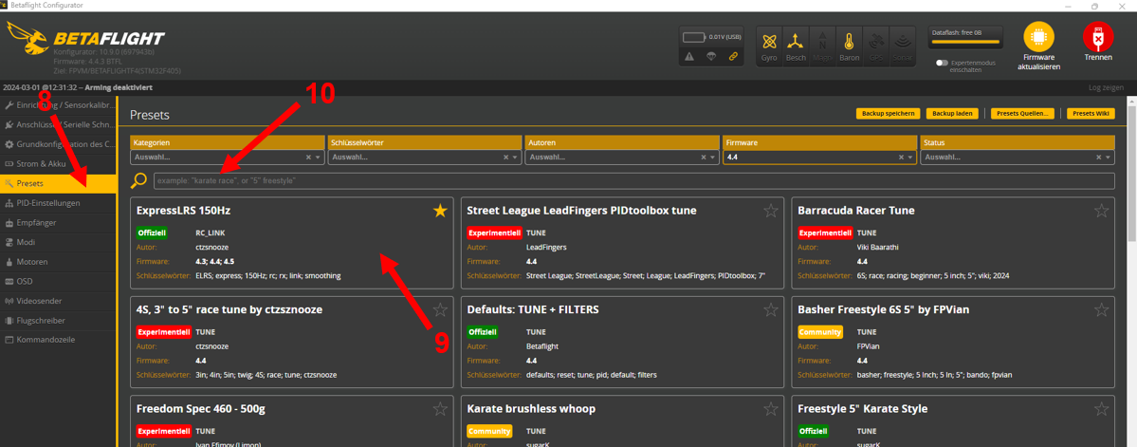
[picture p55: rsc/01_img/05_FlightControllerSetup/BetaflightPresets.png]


Mit Klick auf die Kachel öffnet sich dann ein Fenster in dem du nur noch im Drop-Down-Menü folgende Haken (11) setzen musst:
-	Ultra Cinematic
-	Serial, separate RX
-	Whole Pack values

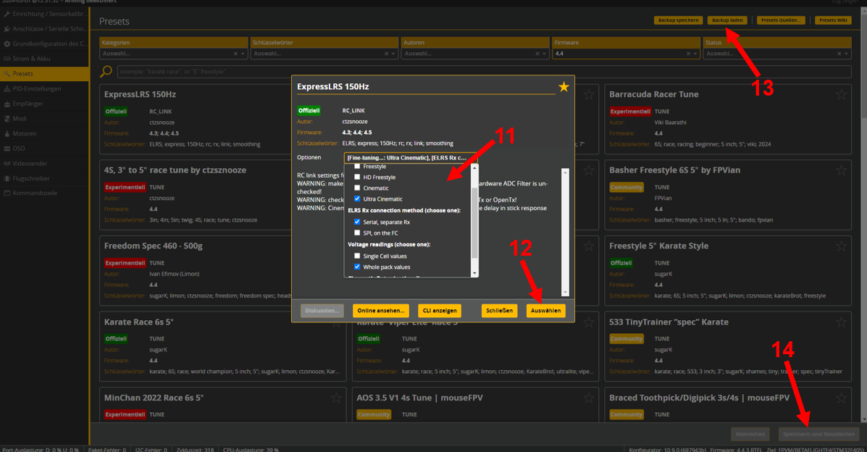
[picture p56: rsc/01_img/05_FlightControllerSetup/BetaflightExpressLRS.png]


Wenn du die Haken gesetzt hast, dann kannst du auf _Auswählen_ (12) drücken. Anschließend laden wir noch ein paar Einstellungen, die schon extra für dich vorbereitet wurden, indem du auf _Backup laden_ (13) drückst. Du wirst dann aufgefordert eine passende Datei auszuwählen. Du findest sie [hier](/rsc/03_software/01_betaflight) mit dem Namen _Backup_Drohne.txt_. Um sie im *Betaflight Configurator* öffnen zu können musst du sie zuerst aus Git downloaden. Klicke dazu auf die zwei unten markierten Schaltflächen.

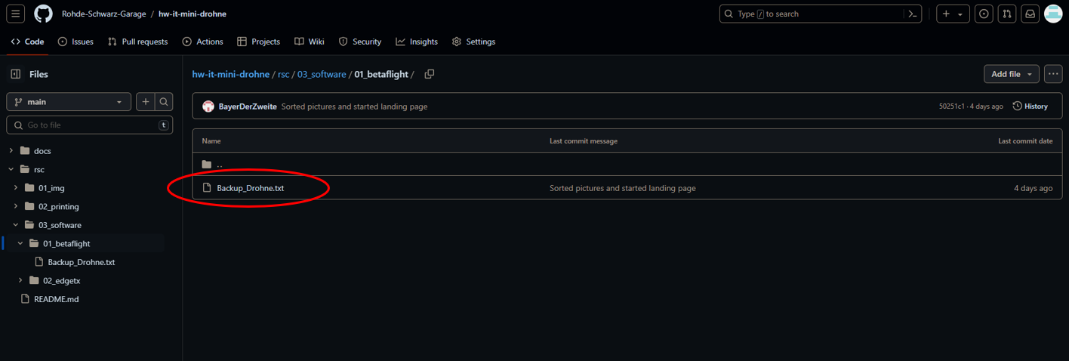
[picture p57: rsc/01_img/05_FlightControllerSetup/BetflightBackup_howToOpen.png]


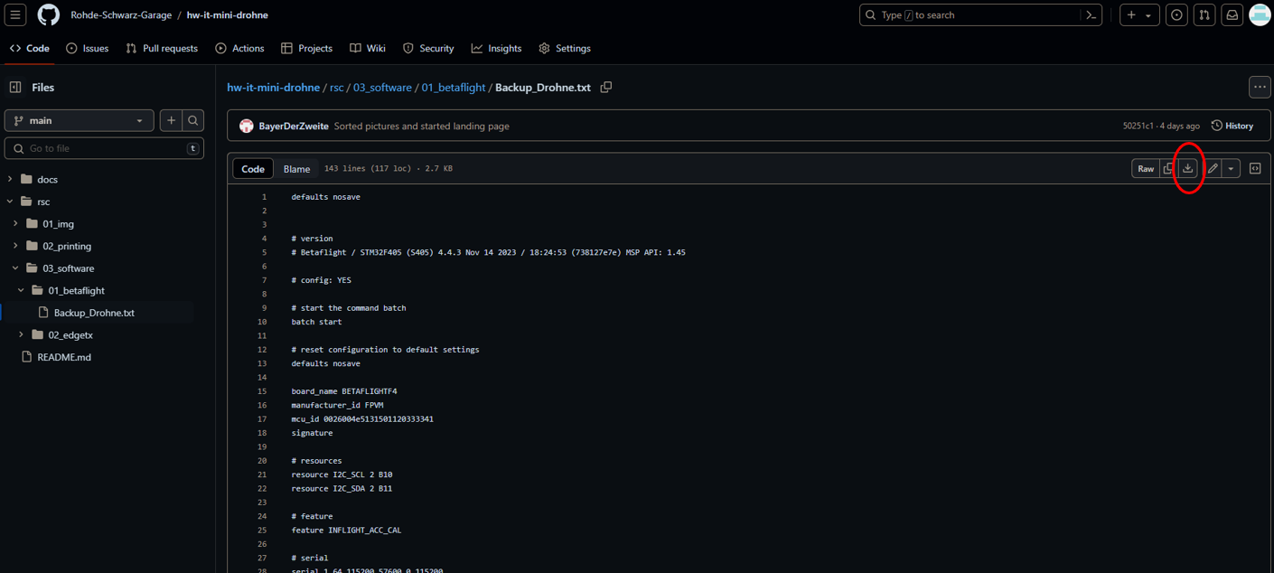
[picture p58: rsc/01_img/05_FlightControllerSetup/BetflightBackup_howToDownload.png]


Wenn du diese Backup-Datei im *Betaflight Configurator* geöffnet hast, dann kannst du auf Speichern und _Neustarten_ (14) drücken. Der Flight Controller startet nun neu und wird sich gleich darauf wieder automatisch verbinden.

Damit sind wir fürs erste mit dem Flight Controller selbst fertig. Bitte lies nun unbedingt **zuerst** die [Sicherheitshinweise](/docs/09_Safety.md) und fahre **erst dann** mit der weiteren Einrichtung fort.

# Konfiguration Motorsteuerung


Als nächstes konfigurieren wir die ESCs, also die Motorsteuerung.

>Wie in der grundlegenden Beschreibung der Drohne (2.1) erwähnt sind die ESCs (Electronic Speed Controller) dafür verantwortlich die Energie so an die Motoren zu leiten, wie es der Flight Controller vorgibt. Um das korrekt ausführen zu können, müssen die ESCs aber einige Parameter übergeben bekommen. Genau das machen wir in diesem Kapitel.

Entferne den Akku vom Ladegerät und verbinde ihn mit der Drohne. Lass dich nicht verunsichern, ein eventuelles Piepsen der Drohne beim Anstecken des Akkus ist ganz normal. Verbinde dann die Drohne per USB-Kabel an den PC. Vergiss dabei nicht, wieder den Lüfter auf die Drohne zu richten. Öffne im Browser [esc-configurator.com](https://esc-configurator.com). Achte darauf, dass sowohl der _Betaflight Configurator_ als auch der _ExpressLRS Configurator_ geschlossen sind, während du im _ESC Configurator_ arbeitest. Außerdem muss die Fernbedienung ausgeschaltet sein. Das Browser-Fenster sollte wie unten aussehen.

Port und Baud-Rate rechts oben (1) sollten schon automatisch vorausgewählt sein. Falls sie nicht vorausgewählt sind, dann gehe auf _Seriellen Port wählen_ und wähle _Betaflight STM32_ aus. Anschließend kannst du auf _Verbinden_ (2) drücken.

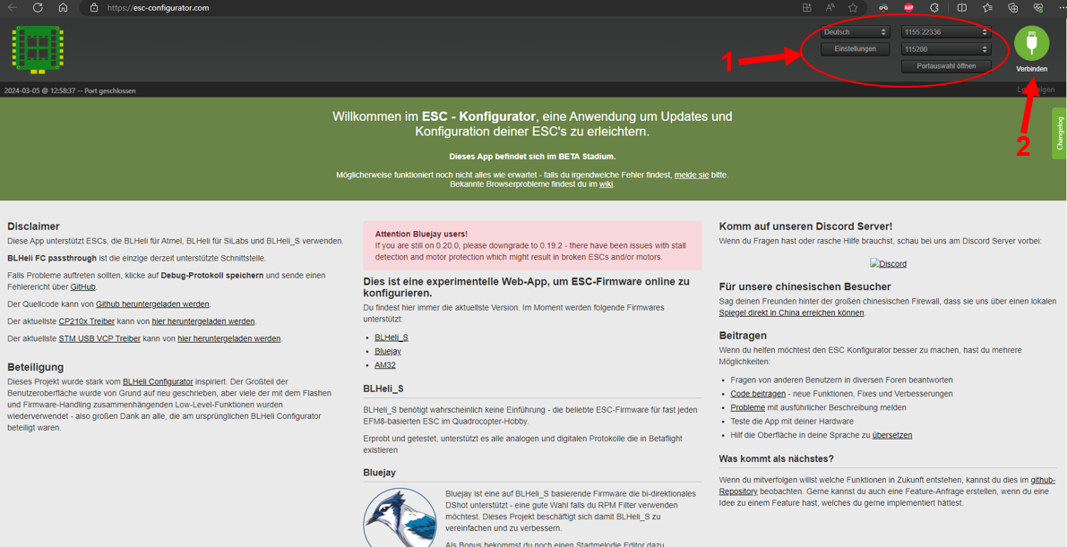
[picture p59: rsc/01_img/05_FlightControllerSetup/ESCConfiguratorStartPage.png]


Drücke dann _Einstellungen lesen_ (3), um die aktuellen Parameter der Motoren auszulesen. Wenn hier ein Fehler auftritt oder die Einstellungen einfach nicht ausgelesen werden, dann empfiehlt sich mittels _Zadig_ etwaige fehlende Treiber nochmals zu installieren (siehe [Installation Software und Treiber](/docs/01_Materials.md#software)).

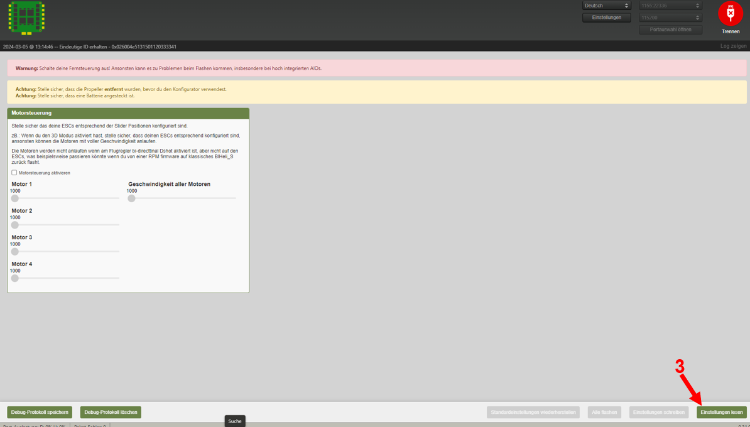
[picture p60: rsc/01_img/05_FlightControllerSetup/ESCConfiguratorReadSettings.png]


Im nächsten Fenster werden wir nun die eigentlichen Einstellungen vornehmen. Wundere dich nicht, wenn bei dir die angezeigten Werte/Parameter noch nicht mit dem Fenster aus dem Screenshot übereinstimmen, wir werden diese erst noch einstellen. Zuerst musst du aber noch die richtige Firmware auf die ESCs flashen. Drücke auf _Alle flashen_ (4), um also alle vier ESCs zu flashen.

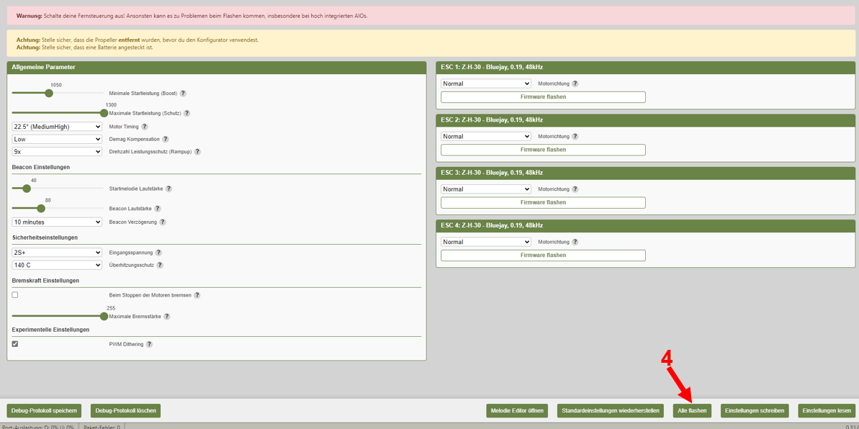
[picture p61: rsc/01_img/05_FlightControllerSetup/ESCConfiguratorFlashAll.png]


Im Fenster, das sich dann öffnet, wählst du in den Dropdown-Menüs (5) für _Firmware_, _ESC_, _Version_ und _PWM Frequency_ die Einträge aus dem Bild unten aus und drückst dann auf _Flashen_ (6).

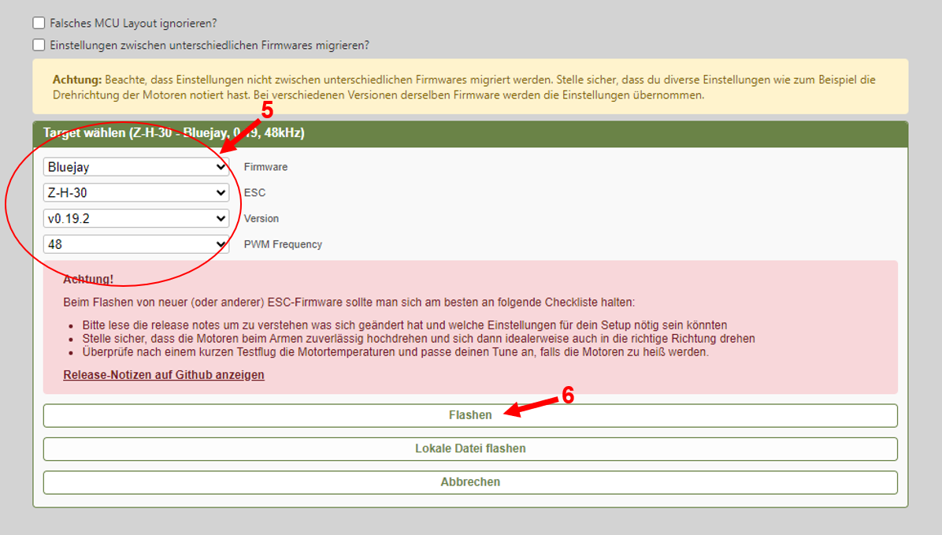
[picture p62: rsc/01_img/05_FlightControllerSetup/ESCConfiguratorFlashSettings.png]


Das Fenster wird dann wieder auf das vorherige zurückspringen und du kannst beobachten wie die ESCs nacheinander geflashed werden. (7)

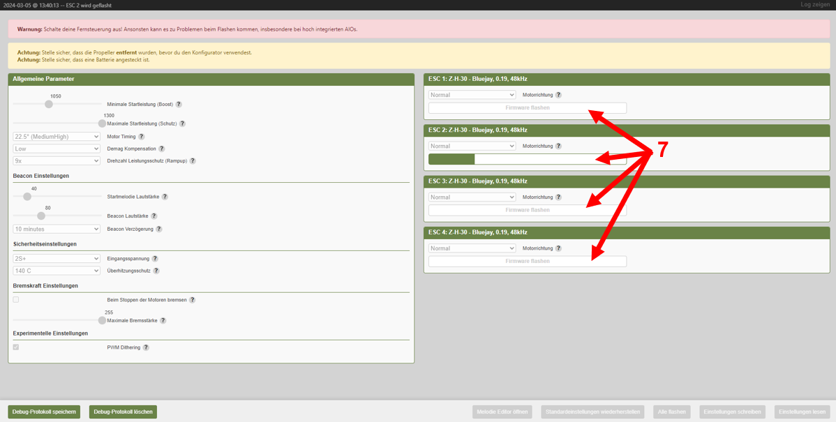
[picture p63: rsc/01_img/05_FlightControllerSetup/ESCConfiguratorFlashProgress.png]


Sobald die Buttons unten rechts nicht mehr ausgegraut sind, ist das Flashen beendet. Überprüfe, ob die Firmware der ESCs bei dir genauso lautet wie in (8), dann kannst du fortfahren. Jetzt musst du jeden einzelnen Parameter auf der linken Seite (9) auf die Werte im Screenshot anpassen. Bist du fertig, dann drücke _Einstellungen schreiben_ (10), um die Parameter auf den ESCs zu speichern.

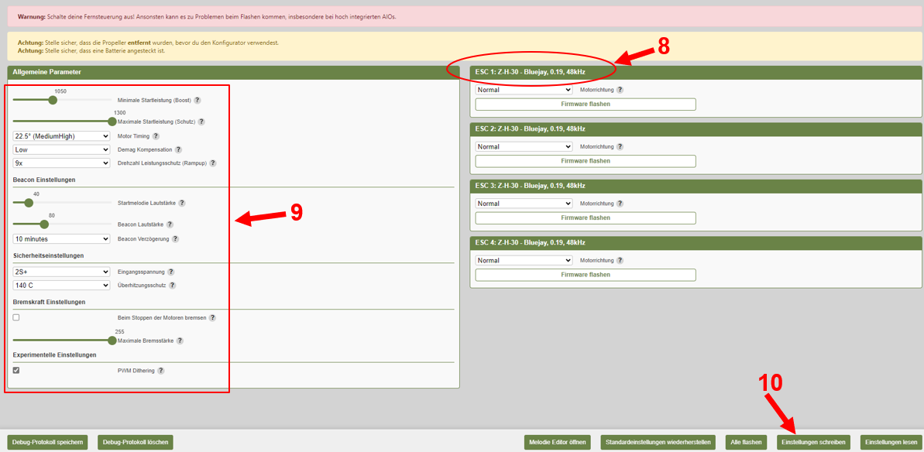
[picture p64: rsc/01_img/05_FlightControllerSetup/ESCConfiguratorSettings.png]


Schließe den Browser und öffne den _Betaflight Configurator_. Verbinde dich mit dem Flight Controller und klicke auf den Reiter _Motoren_ (11). Was wir jetzt noch anpassen müssen, ist die Standard-Drehrichtung der Motoren. Du kannst dich dabei an der Grafik (12) orientieren.Um herauszufinden, wie die Motoren aktuell drehen, wirst du nacheinander die Motoren ganz leicht drehen lassen. Du wirst einen kleines Stück Papier vorsichtig in die Propeller halten. Anhand dessen, in welche Richtung das Papier dabei vom Propeller gedrückt wird, kannst du erkennen in welche Richtung der Propeller dreht. Versuch nicht, es nur mit bloßem Auge ohne den Trick mit dem Stück Papier zu erkennen. Man vertut sich leider sehr schnell, was dann aber einen stabilen Flug der Drohne unmöglich macht.

**Wichtig:** Achte darauf keine Haare/Schals/Finger/o.ä. in die Propeller zu halten, während sie sich drehen oder generell während der Akku der Drohne angesteckt ist.

Um die Motoren einzeln drehen zu lassen musst du den Schalter (13) aktivieren. Achtung: Ab jetzt sind die Motoren aktiviert! Entgegen dem Hinweis in dem Kasten darüber entfernen wir nicht die Propeller. Sie sind erstens sehr klein, daher ist das Verletzungsrisiko generell nicht ganz so groß, wie bei größeren Drohnen. Zweitens sind auch die Achsen der Motoren, auf denen die Propeller aufgesteckt sind, sehr klein, weshalb sie nicht so geeignet sind, um die Propeller oft auf- und abzustecken.

Bewege nun einzeln die Regler (14) **vorsichtig** nach oben, bis sich der jeweilige Motor **langsam (nicht mehr!)** dreht und befolge die Schritte mit dem Papierstück von oben. Markiere in der Grafik (12) z.B. mit einem Kreuz, welche(n) der Motoren du umkehren musst, damit sie in die richtige Richtung drehen.





Wenn du herausgefunden hast, welche Motoren du umkehren musst, dann drücke Motoren stoppen (15) und schließe den Betaflight Configurator. Öffne wieder Microsoft Edge, verbinde dich im ESC Configurator mit der Drohne und lies die Einstellungen aus. Jetzt solltest du wieder auf der Seite von zuvor sein. Es bleibt nun nur noch die Motoren, die du eben ermittelt hast, zu reversen (16).

**Wichtig:** Hier musst du **deine** Konfiguration übernehmen. Es könnten bei dir also beispielsweise auch die Motoren 1&2 oder 2&4 _reversed_ sein.

Zum Schluss musst du nur noch die _Einstellungen schreiben_ (17). Um sicherzugehen, kannst du die Steps im _Betaflight Configurator_ wiederholen und überprüfen, ob sich die Motoren jetzt in die richtige Richtung drehen.



# Konfiguration Empfangsmodul


Bevor wir zum Jungfernflug deiner Drohne kommen können, ist der letzte Schritt noch das Empfangsmodul zu konfigurieren. Den Akku kannst du wieder von der Drohne trennen. Er ist nur nötig, um die Motoren drehen zu lassen. Für alles andere genügt die Spannungsversorgung per USB. Analog zur [Konfiguration Übertragungsmodul](/docs/03_RemoteSetup.md#konfiguration-übertragungsmodul) verwenden wir wieder den _ExpressLRS Configurator_. Achte darauf, dass sowohl _Betaflight Configurator_ und _ESC Configurator_ geschlossen, sowie außerdem die Fernbedienung ausgeschaltet ist.

Schließe die Drohne per USB-Kabel am PC an. Öffne den _ExpressLRS Configurator_. Triff dort die Einstellungen (1,2,3) so wie im untenstehenden Screenshot. Sobald du das getan hast, sollten die meisten der Einstellungen im roten Kasten (4) automatisch richtig erscheinen. Falls sie das nicht tun, korrigiere sie bitte entsprechend. Lediglich bei der _Binding Phrase_ (5) musst du aufpassen. Hier gilt es dieselbe Binding Phrase einzutragen, die du im Übertragungsmodul der Fernbedienung (siehe [Konfiguration Übertragungsmodul](/docs/03_RemoteSetup.md#konfiguration-übertragungsmodul)) vergeben hast!





Sobald du alle Einstellungen getroffen hast, musst du nur noch auf _Auf Gerät Installieren_ (6) drücken. Dann startet die Installation und wird am Ende mit Operation erfolgreich abgeschlossen quittiert. Kommt es zu Fehlern, liegt es wahrscheinlich an fehlenden Treibern, die du per _Zadig_ nachinstallieren kannst (siehe [Installation Software und Treiber](/docs/01_Materials.md#installation-zadig-usb-treiber)). Kontrolliere außerdem, ob alle anderen Programme geschlossen sind und der richtige COM-Port ausgewählt ist.

Du kannst den _ExpressLRS Configurator_ jetzt schließen.

Stecke die Drohne vom PC ab und dann wieder an. So triggerst du ein erneutes Suchen nach Fernbedienungssignalen. Schalte auch die Fernbedienung wieder an. Sie sollte sich nun automatisch mit dem Empfangsmodul auf dem Flight Controller verbinden.

Als Check, ob alles geklappt hat, solltest du jetzt nochmal den _Betaflight Configurator_ öffnen. Verbinde die Drohne genauso, wie du es mittlerweile schon kennst. Im Reiter _Empfänger_ (7) solltest du in den Balken (8) jetzt die Änderungen der Werte live verfolgen können, wenn du die Sticks auf der Fernbedienung bewegst.



## [Klicke hier, um zurück zur Übersicht der Kapitel zu kommen!](/README.md#kapitel)

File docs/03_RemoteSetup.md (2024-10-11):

# Navigation und Einrichtung Fernbedienung


## Wichtig

Die **vorhandene Fernsteuerung in der Garage ist bereits mit den Standard-Einstellungen aus diesem Kapitel konfiguriert**. Insbesondere die Bindungsphrase ist gemäß der Anleitung konfiguriert. **Somit musst du die Schritte aus dem Kapitel *Navigation und Einrichtung Fernsteuerung* nicht mehr ausführen.**  

Sollte in späteren Schritten der Anleitung die Drohne keine Verbindung mit der Fernbedienung aufbauen können, so kannst du dieses Kapitel sicherheitshalber bearbeiten, um eine mögliche Fehlerquelle auszuschließen.

Es empfiehlt sich dennoch das Kapitel aufmerksam zu lesen. Nimmst du die Drohne mit Nachhause und kaufst dir eine eigene Fernbedienung musst du den Schritten mit deiner neuen Fernbedienung folgen.

## Einlegen der Batterien und Aktivieren der selbstständigen Zentrierung

Nach dem Entfernen der gummierten Griffschalen kannst du mit einem Torx 7 oder 2mm Innensechskantschlüssel die selbstständige Zentrierung des Schubreglers aktivieren. Drehe hierfür die mit `1` markierte Schraube entgegen dem Uhrzeigersinn, bis sich der dazugehörige Gimbal federgestützt in der Mittelposition hält.  
Falls das Gimbal noch nicht selbst die Mittelposition hält, drehe die mit `2` markierte Schraube im Uhrzeigersinn, bis sich der dazugehörige Gimbal federgestützt in der Mittelposition hält.

Nun kannst du die zwei 18650 Li-Ion Batterien einlegen. Achte dabei auf die **korrekte Polung**, wie sie in dem Bild markiert ist.



## Übersicht der wichtigen Tasten

In der Anleitung wirst du nicht alle Tasten brauchen, aber es ist nützlich, sich einen groben Überblick über die allgemeinen Funktionen zu verschaffen:



# Aktualisieren Fernbedienung

Da die Firmwareversion der Fernbedienung vom Herstellungsdatum abhängig ist, musst du zuerst die korrekte Firmware installieren.

Dafür schaltest du die Fernbedienung aus, falls diese an ist, und verbindest den oberen USB-C Anschluss mit deinem PC. Anschließend öffnest du den [EdgeTX Buddy](https://buddy.edgetx.org/#/flash?version=v2.10.2) und wählst die im Bild markierten Einstellungen aus.



Wähle nun *Flashen über USB* aus und klicke auf *Neues Gerät hinzufügen*. Dort findest du den Bootloader der Fernsteuerung mit dem Namen *STM32 BOOTLOADER* und wählst ihn aus.



Klicke nun auf *Weiter* und dann auf *Beginne mit dem Flashen*. Dieser Prozess kann ein paar Minuten dauern. Trenne die Fernsteuerung unter keinen Umständen von deinem PC bis das Flashen fertiggestellt ist.

# Einrichten Fernbedienung


Damit die Fernbedienung das tut, was du möchtest, muss sie konfiguriert werden. Die nötigen Konfigurationen liegen schon auf dem PC, die folgenden Schritte zeigen dir, wie du diese auf die Fernbedienung ziehen kannst.

Schalte den PC und die Fernbedienung an.

Als Nächstes nimmst du das USB-C Kabel und verbindest den PC und die Fernbedienung miteinander. Achte darauf, dass du das Kabel oben bei der Fernbedienung einsteckst.

Beim Einstecken sollte ein Fenster mit drei verschiedenen Auswahlmöglichkeiten erscheinen. Wähle mit dem Drehrad rechts die Option „USB-Storage“ und drücke das Drehrad. Wenn du versehentlich etwas anderes ausgewählt hast, steck das Kabel einfach wieder ein und aus und wiederhole den Vorgang.



Klicke [hier](https://download-directory.github.io/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) und es wird automatisch ein komprimierter Ordner mit den Konfigurationen heruntergeladen.  Entpacke den Ordner und kopiere die enthaltenen Dateien (STRG+C oder Rechtsklick -> Kopiersymbol).

Wähle nun links unten das USB-Laufwerk der Fernbedienung aus.



**Lösche alle enthaltenen Dateien und Ordner.** Im Anschluss fügst du die heruntergeladenen Ordner ein (STRG+V oder Rechtsklick -> Einfüge Symbol).  

Warte nun, bis der Vorgang abgeschlossen wurde. Anschließend trennst du das USB-Kabel von der Fernsteuerung und startest diese neu. Durch den Neustart werden die geänderten Konfigurationen eingelesen.  

Falls es zu einem Speicherfehler auf der Fernsteuerung kommt, bestätige durch das mehrmalige Drücken des Drehrads, dass eine Backup-Konfiguration geladen werden soll. Anschließend verbindest du die Fernsteuerung wieder mit dem PC und wählst USB-Storage aus.  
Wähle das Laufwerk der Fernbedienung aus und navigiere zu dem Ordner `Models`. In diesem löschst du die Datei mit der Endung `.yaml` und fügst die Datei `model00.yaml` aus dem heruntergeladenen Ordner ein.

Glückwunsch, du hast die benötigte Konfiguration auf die Fernbedienung übertragen. Im weiteren Verlauf wirst du nun einige Zusatzeinstellungen vornehmen.

## Kalibrieren Sticks

> In EdgeTX ist es wichtig, die Gimbals zu kalibrieren, um eine präzise Steuerung deiner Drohne sicherzustellen. Die Kalibrierung stellt sicher, dass die Mittelpositionen der Sticks korrekt erkannt werden und die Bewegungsbereiche der Gimbals optimal eingestellt sind. Wenn du beispielsweise neue Gimbals in deinem Sender verwendest oder merkst, dass die Mittelpositionen nicht genau sind, solltest du die Kalibrierung durchführen. Achte darauf, die Gimbals bei der Kalibrierung in einer geraden Linie von links nach rechts und von oben nach unten zu bewegen, ohne übermäßigen Druck an den Endpunkten auszuüben. Dieser Schritt ist besonders wichtig, um eine stabile und präzise Steuerung deiner Drohne zu gewährleisten.

Schalte hierfür die Fernsteuerung ein und drücke den **SYS**-Knopf. Navigiere mittels **PAGE>** bis zur Seite *HARDWARE* und bestätige die Auswahl von *Calibration* durch drücken des Drehrads.

Achte nun darauf die Sticks nicht zu berühren und drücke aud das Drehrad um den Prozess zu starten. Drücke nochmals das Drehrad um die Mittelpunkte der Achsen festzulegen.

Im Anschluss bewegst du die Sticks mehrmals in alle Richtungen bis zum Anschlag, ohne viel Kraft aufzuwenden. Wenn du damit fertig bist klicke auf das Drehrad um die Kalibrierung zu beenden. Durch das mehrmalige Drücken des **RTN**-Knopfes gelangst du wieder auf die Startseite.

# Konfiguration Übertragungsmodul


Damit sich die Fernbedienung mit der Drohne verbinden kann, müssen wir das Übertragungsmodul konfigurieren.

Zuerst starten wir die Fernbedienung mit einem langen Druck auf den Power Button bis das *EdgeTX*-Logo erscheint. Verbinde anschließend die Fernbedienung per USB-Kabel mit dem PC. Nimm dazu den oberen Anschluss an der Fernbedienung.

Es sollte dann folgende Anzeige auf der Fernbedienung erscheinen. Wähle mit dem Drehrad durch Drehen *USB-Serial (VCP)* (1) aus und bestätige durch Drücken des Drehrads.



Öffne dann die Software *ExpressLRS Configurator*. Du findest sie im Ordner Drohne auf dem Desktop.
Das Fenster, das sich öffnet, sieht etwa so wie unten aus. Wähle die Werte so wie in (2,3,4) aus.



Anschließend sollten die Werte unten im roten Kasten automatisch ausgewählt werden. Falls nicht, vervollständige sie bitte entsprechend. Die *Binding Phrase* (5) kannst du **frei wählen**. Du musst lediglich darauf achten, dass, falls mehrere Drohnen gleichzeitig gebaut werden, nicht mehrmals die gleiche Binding Phrase verwendet wird. Sprich dich also mit anderen Drohnenpiloten ab, sonst kann es zu Verbindungsfehlern kommen und niemand kann fliegen!

Zuletzt musst du nur noch im Dropdown-Menü (6) *COM5* auswählen. Möglicherweise ist die Zahl hinter *COM* nicht 5, sondern eine andere Zahl. Das macht nichts. Im Dropdown-Menü sollte es nur eine Auswahlmöglichkeit geben, die nimmst du einfach. Gibt es mehr als eine Auswahlmöglichkeit, ist das ein Zeichen dafür, dass noch irgendein anderes Gerät am PC angesteckt ist, das gerade nicht benötigt wird. Entferne es und öffne das Dropdown-Menü neu, dann sollte nur noch eine Möglichkeit übrigbleiben.

Solltest du an diesem Punkt nicht weiterkommen liegt es möglicherweise an nicht installierten Treibern. In diesem Fall gehst du wie [hier](/docs/01_Materials.md#installation-zadig-usb-treiber) beschrieben vor und installierst die Treiber per *Zadig*.  
Falls dies nicht funktioniert musst du den STM32-Treiber installieren oder eine bestehende Installation reparieren. Folge dazu [dieser](/docs/01_Materials.md#installation-stm32-virtual-com-port-treiber) Anleitung.

Anschließend kannst du die Konfiguration auf die Fernbedienung übertragen, indem du *Auf Gerät installieren* (7) drückst.



Wenn die Installation fertig ist, kannst du die Fernbedienung abstecken und ausschalten sowie das Programm schließen. Kommt es zu Fehlern, liegt es wahrscheinlich an fehlenden Treibern, die du per *Zadig* nachinstallieren kannst (1.4.1 ).



Nachdem du alles erfolgreich abgeschlossen hast, müssen wir noch eine kleine Änderung an der Fernbedienung machen. Dafür musst du die Fernbedienung starten und zum Startbildschirm gelangen.

Jetzt müssen wir in das System Menü gelangen. Dafür musst du den **SYS-Knopf** drücken. Danach sollte dieses Menü auf dem Bildschirm zu sehen sein: 



Nun haben wir die verschiedenen Tools aufgezählt, die es für den Controller gibt. Um das Übertragungsmodul zu konfigurieren, müssen wir in das Tool **ExpressLRS** gelangen. Mit dem Bestätigen des Drehrads gelangst du in ExpressLRS und solltest diesen Bildschirm sehen:



Nun können wir auch schon die erste Einstellung verändern. Und zwar müssen wir die erste Zeile mit dem Namen **Packet Rate** verändern (im Bild markiert). Diese musst du auf 150Hz einstellen. (Wenn die Paketrate bereits auf **150 Hz** eingestellt ist, kannst du zurück zum Startbildschirm gehen)

## [Klicke hier, um zurück zur Übersicht der Kapitel zu kommen!](/README.md#kapitel)

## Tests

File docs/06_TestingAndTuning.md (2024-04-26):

# Funktionstest


Nachdem wir alles richtig eingestellt haben, kommen wir jetzt zum Funktionstest.

## Grundlegende Steuerung:

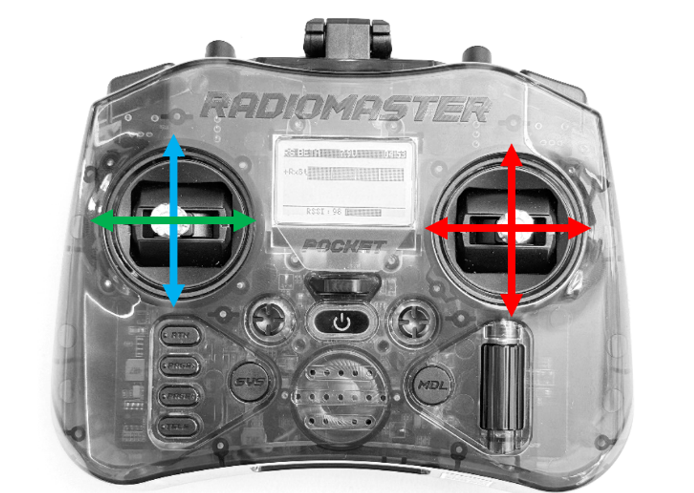
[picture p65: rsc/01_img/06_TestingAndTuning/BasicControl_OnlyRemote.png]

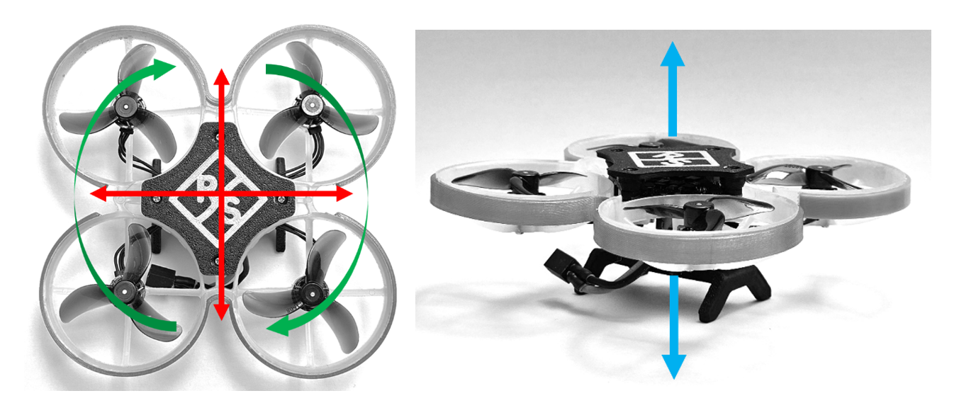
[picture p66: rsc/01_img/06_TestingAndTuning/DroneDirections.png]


Als erstes schaltest du die Fernbedienung ein, bis du wieder den Startbildschirm siehst. Danach steckst du die Batterie der Drohne an die Drohne dran. 
Um die Drohne zu starten, müssen wir erst ein paar Bedingungen erfüllen:

1.	Die Drohne darf nicht an den PC angeschlossen sein 

2.	Die Drohne muss waagrecht auf einer Fläche stehen.  

Nachdem du die Voraussetzungen erfüllt hast kannst du die Drohne starten. Als erstes müssen wir den linken Joystick ganz nach unten drücken und danach musst du den **Arm-Button** drücken. Nun sollten sich schon die Propeller drehen und die Drohne ist bereit zu fliegen. 
Um die Motoren wieder auszuschalten, musst du wieder den **Arm-Button** drücken. Der Prozess des **Armens** wird [hier](/docs/09_Safety.md#sicheres-fliegen) genauer behandelt.

# Tuning


Nachdem du erfolgreich alle Komponenten deiner Drohne getestet hast, folgt ein essenzieller Schritt: das Tuning der Drohne.  
Das erste Ziel wird es sein, dass die Drohne bei zentriertem Schubregler ihre Höhe hält. Des Weiteren soll etwaiges Driften der Drohne während des Fluges ausgeglichen werden, um somit einen stabilen und kontrollierten Flug zu gewährleisten.

>Um das Phänomen des Driftens zu verstehen, ist es notwendig, die Rolle des Beschleunigungssensors innerhalb der Drohnensteuerung zu verdeutlichen. Dieser ist ein Sensor, der dazu dient, Beschleunigungen auf allen drei Achsen (x, y, z) zu messen. Er erfasst die Geschwindigkeitsänderung der Drohne sowie die Anwesenheit der Erdanziehungskraft und ermöglicht es dadurch der Drohne, ihre Lage in Bezug auf die Erdoberfläche zu bestimmen.

>Ein falsch kalibrierter Beschleunigungssensors zeigt die Neigung der Drohne in Bezug zur Erdoberfläche nicht korrekt an. Dies führt dazu, dass die Flugsteuerung versucht, eine falsch wahrgenommene Neigung auszugleichen. Im Ergebnis führt dies zu einem Driften in die entgegengesetzte Richtung der falsch angezeigten Neigung.

>In ähnlicher Weise kann ein nicht richtig getrimmter Beschleunigungssensor dazu führen, dass die Flugsteuerung eine schräge "Ruheposition" annimmt. Dadurch wird auch ohne Steuerbefehle eine Bewegung in Richtung dieser scheinbaren Neigung eingeleitet, was ebenfalls zu einem Driften der Drohne führt.

>Um also ein stabiles und kontrolliertes Flugerlebnis zu gewährleisten, ist es von essenzieller Bedeutung, die Kalibrierung und das Trimming des Beschleunigungssensors exakt durchzuführen. Dies hilft dabei, Driften der Drohne auszugleichen und ermöglicht einen stabilen und präzisen Flug.

## Kalibrierung Beschleunigungssensor und Gyroskop

Bevor du mit dem Trimming des Beschleunigungssensors beginnst, musst du diesen und das Gyroskop kalibrieren. 

>Das Gyroskop ist ein weiterer wichtiger Sensor in deiner Drohne. Es misst die Winkelgeschwindigkeit, also wie schnell sich die Drohne um ihre eigene Achse dreht. Damit sorgt das Gyroskop für Stabilität im Flug und hilft, die Drohne bei Wind oder bei Steuerbefehlen in der gewünschten Lage zu halten. 

### Hier sind die Schritte, die du befolgen musst:

1.	Schalte die Fernbedienung ein.

2.	Schiebe die Batterie in den Einschub an der Drohne und verbinde anschließend die Batterie mit der Drohne. Stelle die Drohne auf eine waagrechte, glatte Fläche.

3.	Prüfe, ob die Drohne vollständig eben auf ihren Standfüßen steht.

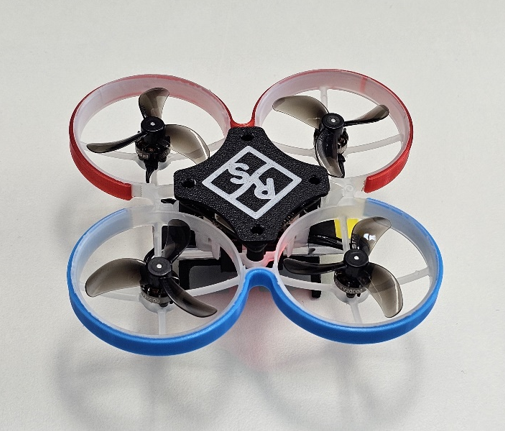
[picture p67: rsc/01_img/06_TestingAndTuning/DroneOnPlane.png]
    

4.  Führe den Stick Befehl für die Gyroskop-Kalibrierung durch, indem du den linken Stick in der linken unteren Ecke und gleichzeitig den rechten Stick unten in der Mitte für einige Sekunden hältst. Auf dem Bild ist die Position der Sticks nochmals dargestellt

    

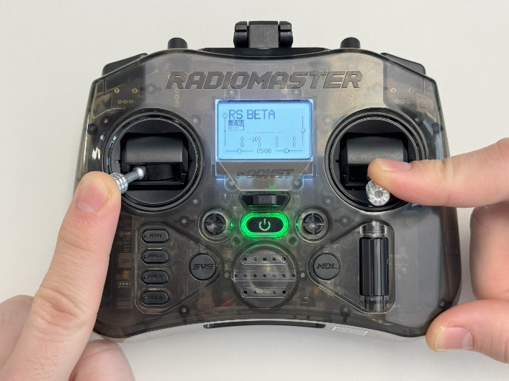
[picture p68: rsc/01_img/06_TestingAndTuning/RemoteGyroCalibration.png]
    

5. Warte einige Sekunden und führe dann den Stick Befehl für die Beschleunigungssensor-Kalibrierung aus, indem du den linken Stick in der linken oberen Ecke und gleichzeitig den rechten Stick unten in der Mitte für einige Sekunden hältst.

    

6.  Führe einen kurzen Flugtest durch. Dafür armst du die Drohne (wie vorhergehend in den Sicherheitshinweisen beschrieben) und gibst Schub bis die Drohne abhebt und schwebt, ohne sie durch den Raum zu steuern. Ein leichtes Driften oder ungleichmäßiges Halten der Höhe stört an dieser Stelle nicht. Das werden wir im nächsten Schritt ausgleichen.

Sollte die Drohne sehr unruhig fliegen bietet es sich an die Schritte 1 bis 5 zu wiederholen.

## Trimmen des Schubreglers

>Damit die Drohne ruhig schweben kann muss sie eine gewisse Menge an Schub erzeugen, der ihr Eigengewicht ausgleicht. Dieser Schub soll erzeugt werden, wenn der Schubregler an der Fernsteuerung sich in der Mittelposition befindet. Um dies zu erreichen, wird durch Trimmen der an die Drohne übertragene Wert für den Schubregler verschoben, während die physische Position des Sticks gleich bleibt.

### Vorbereitung vor dem Trimmen:

Zuerst musst du sicherstellen, dass nicht aus Versehen Trimm eingestellt wurde während den vorhergegangenen Schritten. Vergleiche dazu das Display der Fernsteuerung mit der Abbildung und korrigiere mit dem entsprechenden Trimm-Reglern, bis alle Balken symmetrisch sind.

Kontrolliere zusätzlich, dass der Akku mindestens halb voll ist.
>Ist der Akku weniger als halb voll, so ist die Leistungsabgabe etwas vermindert. Folglich ist auch etwas mehr Schub nötig, um die Drohne in der Luft zu halten. Für ein möglichst unverfälschtes Trimm-Ergebnis sollte also der Akku mindestens halb voll sein.

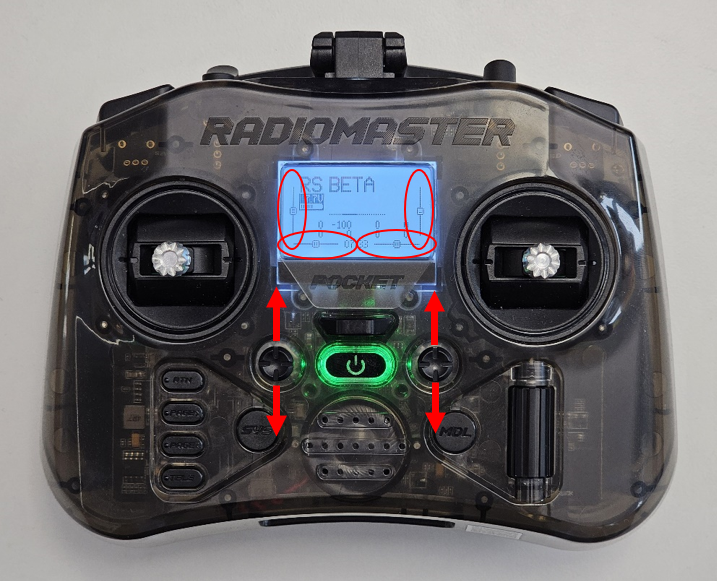
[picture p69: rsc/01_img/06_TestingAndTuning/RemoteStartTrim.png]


### Das eigentliche Trimmen:

1.	Schalte die Fernsteuerung an und verbinde die Drohne wie bereits vorhergehend beschrieben mit dem Akku. Stelle die Drohne anschließend in die Raummitte.

2.	Arme die Drohne und führe den Schubregler in die Mitte, bis er die neutrale Position erreicht.

3.	Wenn die Drohne an Höhe verliert oder gar nicht erst abhebt, trimme den Schubregler nach oben. Wenn die Drohne stetig an Höhe gewinnt, trimme Schubregler nach unten. Dafür bewegst du den Trimm-Regler in die entsprechende Richtung und fügst somit eine Einheit Trimm hinzu. Der Vorgang lässt sich beliebig wiederholen und summiert somit den Trimm auf.  
Den Regler zum Trimmen findest du auf der Fernsteuerung, wie auf dem Bild ersichtlich. Das Trimmen des Schubreglers ist auch während dem Flug möglich, um die Auswirkungen direkt zu sehen.

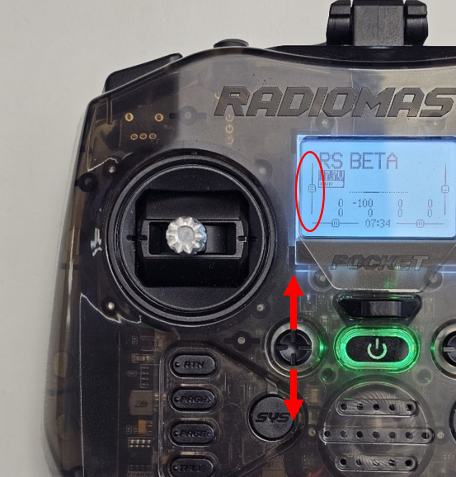
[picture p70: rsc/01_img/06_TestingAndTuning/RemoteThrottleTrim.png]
    

4.	Trimme so lange, bis die Drohne ihre Höhe selbstständig hält. Das kann etwas Geduld erfordern aber lohnt sich am Ende.

## Trimmen des Beschleunigungssensors

### Stickbefehle für das Trimmen:

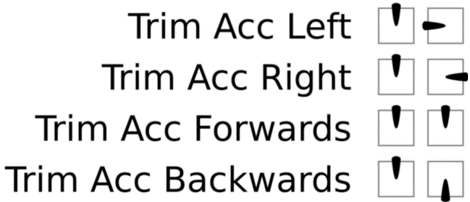
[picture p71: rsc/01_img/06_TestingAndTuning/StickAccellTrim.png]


>Turbulenzen bezeichnen Luftunruhen, die durch die Nähe von Gegenständen oder Wänden erzeugt werden. Diese können die Flugfähigkeit und -stabilität deiner Drohne erheblich beeinflussen, da sie die durch die Propeller produzierten Luftströme stören. Daher kann das Schweben in der Nähe von Wänden oder Gegenständen deine Einschätzung zur Schwebestabilität verfälschen. Stelle beim Trimmen sicher, dass deine Drohne möglichst weit von Gegenständen entfernt in der Mitte des Raums schwebt.

### Hier sind die Schritte, die du befolgen musst:

1.	Nachdem du deine Drohne sicher in die Mitte des Raums gebracht hast, lass sie schweben und beobachte, in welche Richtung sie driftet. Während des Prozesses solltest du darauf achten, den rechten Stick so wenig wie möglich zu benutzen. Sollte die Drohne nach links driften, wird dies durch ein Trimmen nach rechts ausgeglichen.

2.	Sobald du die Richtung des Driftens ermittelt hast, lande die Drohne und deaktiviere die Motoren ("Disarm").

3.	Als nächstes, führe den Stick Command, wie in der Darstellung ersichtlich, aus, um den Beschleunigungssensor in die entgegengesetzte Richtung des Driftens zu trimmen.  
**Für unser Beispiel bedeutet dies:** Wenn die Drohne nach links driftet, führe den Stick Command für ein Trimmen nach rechts aus. Dies trimmt um eine Einheit nach rechts, ein mehrmaliges Wiederholen ist möglich und summiert die Einheiten auf.

4.	Lasse die Drohne erneut schweben und überprüfe, ob noch Drift auftritt. Sollte die Drohne nun gleichmäßig schweben, hast du das Trimmen erfolgreich abgeschlossen. Falls noch Drift vorhanden ist, wiederhole die Schritte, bis die Drohne stabil schwebt.

Das korrekte Trimmen des Beschleunigungssensors ist eine wichtige Fähigkeit, die dir dabei helfen wird, die volle Kontrolle über deine Drohne zu erhalten und das bestmögliche Flugerlebnis zu erzielen. Es verlangt Geduld und Genauigkeit, aber die Belohnung einer gut abgestimmten Drohne ist es definitiv wert.

## Spaß haben

Herzlichen Glückwunsch, deine Drohne ist nun voll flugfähig!

Um deine Flugkünste zu trainieren kannst du dir noch selbst etwaige Szenarien überlegen. Beispielsweise ein Slalom-Kurs, durch den du fliegen musst, ohne die Pylonen zu berühren. Als Pylonen lassen sich dabei wunderbar Stühle missbrauchen, sowohl oberhalb der Sitzflächen die Stuhllehnen als auch die Stuhlbeine unterhalb. Deiner Fantasie sind keine Grenzen gesetzt. Viel Spaß!

## [Klicke hier, um zurück zur Übersicht der Kapitel zu kommen!](/README.md#kapitel)

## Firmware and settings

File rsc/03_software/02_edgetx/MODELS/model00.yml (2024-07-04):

semver: 2.10.2
header: 
   name: "RS BETA"
   modelId: 
      0:
         val: 30
timers: 
   0:
      start: 0
      swtch: "NONE"
      value: 0
      mode: OFF
      countdownBeep: 0
      minuteBeep: 0
      persistent: 0
      countdownStart: 0
      showElapsed: 0
      extraHaptic: 0
      name: "ARM"
telemetryProtocol: 0
thrTrim: 0
noGlobalFunctions: 0
displayTrims: 0
ignoreSensorIds: 0
trimInc: 0
disableThrottleWarning: 1
displayChecklist: 0
extendedLimits: 0
extendedTrims: 0
throttleReversed: 0
enableCustomThrottleWarning: 0
disableTelemetryWarning: 0
showInstanceIds: 0
checklistInteractive: 0
customThrottleWarningPosition: 0
beepANACenter: 0
mixData: 
 -
   weight: 100
   destCh: 0
   srcRaw: I0
   carryTrim: 0
   mixWarn: 0
   mltpx: ADD
   speedPrec: 0
   offset: 0
   swtch: "NONE"
   flightModes: 000000000
   delayUp: 0
   delayDown: 0
   speedUp: 0
   speedDown: 0
   name: ""
 -
   weight: 100
   destCh: 1
   srcRaw: I1
   carryTrim: 0
   mixWarn: 0
   mltpx: ADD
   speedPrec: 0
   offset: 0
   swtch: "NONE"
   flightModes: 000000000
   delayUp: 0
   delayDown: 0
   speedUp: 0
   speedDown: 0
   name: ""
 -
   weight: 100
   destCh: 2
   srcRaw: I2
   carryTrim: 0
   mixWarn: 0
   mltpx: ADD
   speedPrec: 0
   offset: 0
   swtch: "NONE"
   flightModes: 000000000
   delayUp: 0
   delayDown: 0
   speedUp: 0
   speedDown: 0
   name: ""
 -
   weight: 100
   destCh: 3
   srcRaw: I3
   carryTrim: 0
   mixWarn: 0
   mltpx: ADD
   speedPrec: 0
   offset: 0
   swtch: "NONE"
   flightModes: 000000000
   delayUp: 0
   delayDown: 0
   speedUp: 0
   speedDown: 0
   name: ""
 -
   weight: 100
   destCh: 4
   srcRaw: I4
   carryTrim: 0
   mixWarn: 0
   mltpx: ADD
   speedPrec: 0
   offset: 0
   swtch: "NONE"
   flightModes: 000000000
   delayUp: 0
   delayDown: 0
   speedUp: 0
   speedDown: 0
   name: ""
 -
   weight: 100
   destCh: 5
   srcRaw: I5
   carryTrim: 0
   mixWarn: 0
   mltpx: ADD
   speedPrec: 0
   offset: 0
   swtch: "NONE"
   flightModes: 000000000
   delayUp: 0
   delayDown: 0
   speedUp: 0
   speedDown: 0
   name: ""
 -
   weight: 100
   destCh: 6
   srcRaw: I6
   carryTrim: 0
   mixWarn: 0
   mltpx: ADD
   speedPrec: 0
   offset: 0
   swtch: "NONE"
   flightModes: 000000000
   delayUp: 0
   delayDown: 0
   speedUp: 0
   speedDown: 0
   name: ""
 -
   weight: 100
   destCh: 7
   srcRaw: I7
   carryTrim: 0
   mixWarn: 0
   mltpx: ADD
   speedPrec: 0
   offset: 0
   swtch: "NONE"
   flightModes: 000000000
   delayUp: 0
   delayDown: 0
   speedUp: 0
   speedDown: 0
   name: ""
 -
   weight: 100
   destCh: 8
   srcRaw: I8
   carryTrim: 0
   mixWarn: 0
   mltpx: ADD
   speedPrec: 0
   offset: 0
   swtch: "NONE"
   flightModes: 000000000
   delayUp: 0
   delayDown: 0
   speedUp: 0
   speedDown: 0
   name: ""
 -
   weight: 100
   destCh: 9
   srcRaw: I14
   carryTrim: 0
   mixWarn: 0
   mltpx: ADD
   speedPrec: 0
   offset: 0
   swtch: "NONE"
   flightModes: 000000000
   delayUp: 0
   delayDown: 0
   speedUp: 0
   speedDown: 0
   name: ""
 -
   weight: 100
   destCh: 10
   srcRaw: I15
   carryTrim: 0
   mixWarn: 0
   mltpx: ADD
   speedPrec: 0
   offset: 0
   swtch: "NONE"
   flightModes: 000000000
   delayUp: 0
   delayDown: 0
   speedUp: 0
   speedDown: 0
   name: ""
limitData: 
   0:
      min: 0
      max: 0
      ppmCenter: 0
      offset: 0
      symetrical: 0
      revert: 0
      curve: 0
      name: "Y"
   2:
      min: 0
      max: 0
      ppmCenter: 0
      offset: 0
      symetrical: 0
      revert: 0
      curve: 0
      name: "CH 3"
expoData: 
 -
   mode: 3
   scale: 0
   trimSource: 0
   srcRaw: Ail
   chn: 0
   swtch: "NONE"
   flightModes: 000000000
   weight: 100
   name: ""
   offset: 0
   curve: 
      type: 1
      value: 0
 -
   mode: 3
   scale: 0
   trimSource: 0
   srcRaw: Ele
   chn: 1
   swtch: "NONE"
   flightModes: 000000000
   weight: 100
   name: ""
   offset: 0
   curve: 
      type: 1
      value: 0
 -
   mode: 3
   scale: 0
   trimSource: 0
   srcRaw: Thr
   chn: 2
   swtch: "NONE"
   flightModes: 000000000
   weight: 100
   name: ""
   offset: 0
   curve: 
      type: 1
      value: 0
 -
   mode: 3
   scale: 0
   trimSource: 0
   srcRaw: Rud
   chn: 3
   swtch: "NONE"
   flightModes: 000000000
   weight: 100
   name: ""
   offset: 0
   curve: 
      type: 1
      value: 0
 -
   mode: 3
   scale: 0
   trimSource: 0
   srcRaw: SA
   chn: 4
   swtch: "NONE"
   flightModes: 000000000
   weight: 100
   name: ""
   offset: 0
   curve: 
      type: 1
      value: 0
 -
   mode: 3
   scale: 0
   trimSource: 0
   srcRaw: SB
   chn: 5
   swtch: "NONE"
   flightModes: 000000000
   weight: 100
   name: ""
   offset: 0
   curve: 
      type: 1
      value: 0
 -
   mode: 3
   scale: 0
   trimSource: 0
   srcRaw: SC
   chn: 6
   swtch: "NONE"
   flightModes: 000000000
   weight: 100
   name: ""
   offset: 0
   curve: 
      type: 1
      value: 0
 -
   mode: 3
   scale: 0
   trimSource: 0
   srcRaw: SD
   chn: 7
   swtch: "NONE"
   flightModes: 000000000
   weight: 100
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

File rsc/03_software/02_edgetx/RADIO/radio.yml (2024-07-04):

checksum: 23244
manuallyEdited: 0
timezoneMinutes: 0
ppmunit: 0
semver: 2.10.2
board: pocket
calib: 
   LH:
      mid: 997
      spanNeg: 846
      spanPos: 849
   LV:
      mid: 1041
      spanNeg: 762
      spanPos: 785
   RV:
      mid: 1023
      spanNeg: 904
      spanPos: 907
   RH:
      mid: 1006
      spanNeg: 818
      spanPos: 819
   P1:
      mid: 999
      spanNeg: 516
      spanPos: 517
currModel: 0
contrast: 15
vBatWarn: 65
txVoltageCalibration: 0
backlightMode: backlight_mode_all
antennaMode: MODE_PER_MODEL
disableRtcWarning: 0
keysBacklight: 0
dontPlayHello: 0
internalModule: TYPE_CROSSFIRE
trainer: 
   mix: 
      0:
         srcChn: 0
         mode: REPL
         studWeight: 100
      1:
         srcChn: 1
         mode: REPL
         studWeight: 100
      2:
         srcChn: 2
         mode: REPL
         studWeight: 100
      3:
         srcChn: 3
         mode: REPL
         studWeight: 100
view: 19
fai: 0
beepMode: mode_nokeys
alarmsFlash: 0
disableMemoryWarning: 0
disableAlarmWarning: 0
stickMode: 0
timezone: 0
adjustRTC: 0
inactivityTimer: 10
internalModuleBaudrate: 0
splashMode: 0
hapticMode: mode_nokeys
switchesDelay: 0
lightAutoOff: 2
templateSetup: 0
PPM_Multiplier: 0
hapticLength: 2
beepLength: 2
hapticStrength: 2
gpsFormat: 0
audioMuteEnable: 0
speakerPitch: 0
speakerVolume: 18
vBatMin: 60
vBatMax: 80
backlightBright: 0
globalTimer: 3352
bluetoothBaudrate: 0
bluetoothMode: OFF
countryCode: 2
pwrOnSpeed: 0
pwrOffSpeed: 0
noJitterFilter: 1
imperial: 0
disableRssiPoweroffAlarm: 0
USBMode: 0
jackMode: 0
ttsLanguage: "en"
beepVolume: 2
wavVolume: 4
varioVolume: 2
backgroundVolume: 3
varioPitch: 0
varioRange: 0
varioRepeat: 0
serialPort: 
   VCP:
      mode: CLI
      power: 0
potsConfig: 
   P1:
      type: without_detent
      inv: 0
      name: ""
switchConfig: 
   SA:
      type: 2pos
      name: ""
   SB:
      type: 3pos
      name: ""
   SC:
      type: 3pos
      name: ""
   SD:
      type: 2pos
      name: ""
   SE:
      type: toggle
      name: ""
backlightColor: 0
bluetoothName: "98142Q-"
ownerRegistrationID: "MODEL01"
rotEncMode: 0
uartSampleMode: 0
radioGFDisabled: 0
radioTrainerDisabled: 0
modelHeliDisabled: 0
modelFMDisabled: 0
modelCurvesDisabled: 0
modelGVDisabled: 0
modelLSDisabled: 0
modelSFDisabled: 0
modelCustomScriptsDisabled: 0
modelTelemetryDisabled: 0

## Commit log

2024-04-11 Created folder structure and uploaded necessary files
    [BTFL_cli_backup_20240328.txt, Deckplatte.step, Deckplatte.stl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]
2024-04-11 Sorted pictures and started landing page
2024-04-11 Started material
2024-04-11 Finished Materials.md
2024-04-12 Extended safety and FrameAssembly
2024-04-12 Finished FrameAssembly
2024-04-15 Wrote Drone Assembly, Betaflight_Backup_Download
2024-04-15 Wrote drone assembly
2024-04-24 Changed landing page picture
2024-05-03 Added throttle cap to 85% in order to increase useability
2024-06-26 Added location information for battery
2024-07-23 Added printable files for CreatBotF430
    [Markierung_TPU_CreatBotF430.3mf, StandfussDeckplatte_ABSPlus_CreatBotF430.3mf, StandfussDeckplatte_PETG_CreatbotF430.3mf]
